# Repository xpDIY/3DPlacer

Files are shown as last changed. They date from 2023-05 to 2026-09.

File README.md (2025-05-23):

# 3DPlacer
3DPlacer is an adapter to convert 3D printer into pick and place machine that used 
for mounting SMT component into PCB. The aim is to make life easier for people who DIY their PCB 
and doesn't want to spend >$1k. While cost is low, the project still aim to bring enough accuracy
to mount tiny component (ex. 0201, 0402). Also one main goal is to make conversion simple and straight 
forward so that user can switch between 3D printing and PnP function in couple of minutes.
## Features
* Part rotation
* Airpump connectivity
* Adaptability for different 3D printers
  - Ender3 v2
  - Anycubic Mega SE
  - Ender CR10
  - Kingroon kp3s pro s1
* Compatible with openpnp
* Standard Lego style build plate supporting good extendability
* 30+ feeder can be mounted on 220x220mm plate
* 3D printed nozzle tip and JUKI nozzle tip supported
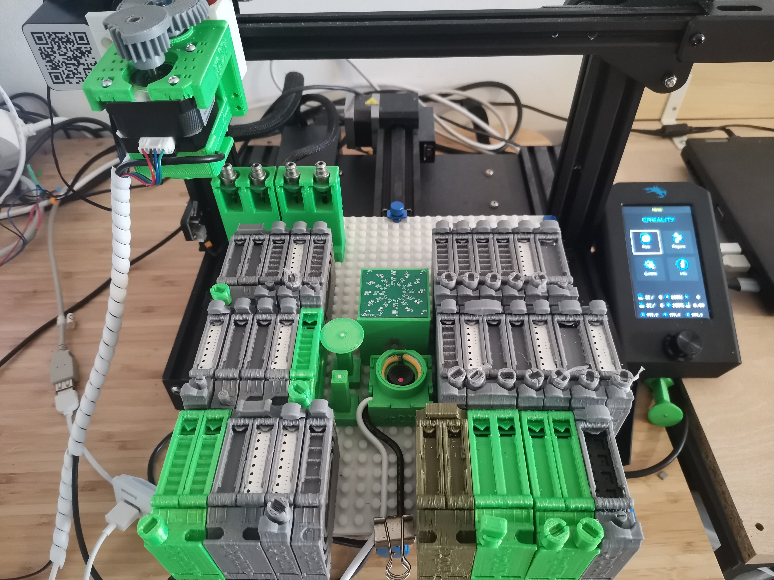
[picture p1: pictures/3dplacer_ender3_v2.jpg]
3DPlacer for Ender3 v2


## Software
* Position aware feature supported
* Both controller and feeder firmware included

### Usage

#### Pre-requsite
* DapLink or other programming interface support ARM M0 MCU with SWD interface
* clang compiler installed

#### Compile
* Enter sw/feeder or sw/control folder
* make clean
* make

#### Flash
* Make sure programmer is connected correctly to SWD interface
* run command `make flash`

## Contribution

Any contribution will be appreciated!

* If you see any bug or improvement, feel free to create a pull request and explain about the pull request

## References

The software project use PY32F0 template project as starting point, please refer to https://github.com/IOsetting/py32f0-template for detailed information.

Thanks and enjoy!

For more info, please refer to https://xpdiy.io
Youtube channel: https://www.youtube.com/@xpdiy

Shield: [][cc-by-nc-sa]

This work is licensed under a
[Creative Commons Attribution-NonCommercial-ShareAlike 4.0 International License][cc-by-nc-sa].

[][cc-by-nc-sa]

[cc-by-nc-sa]: http://creativecommons.org/licenses/by-nc-sa/4.0/
[cc-by-nc-sa-image]: https://licensebuttons.net/l/by-nc-sa/4.0/88x31.png
[cc-by-nc-sa-shield]: https://img.shields.io/badge/License-CC%20BY--NC--SA%204.0-lightgrey.svg

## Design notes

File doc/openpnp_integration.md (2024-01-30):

# This document describe the way to integrate with Openpnp

## General description
In order to integrate with Openpnp, the idea is to provide various G code so that openpnp can use and setup the system. The serial text interface will be used. There are several gcodes currently needed for integration. In the description below, square bracket [] means optional, {} means parameter. 

## System architecture
The system contains openpnp, strip board and components. When user starts job or setup the components in openpnp, ex. feeders, openpnp will fire command (described in section below), then the command string will be passed to strip boards, strip boards will be responbile to pass the strings further to peticular components. The components received the command will then interpret the command and send the response back. The strip board will be used as a tunnel which forward the infomation.
Communication between Openpnp and strip board is serial communication. Strip board can communicate with other strip boards, the protocol used here is I2C. Then under each strip board, there will be multiple components, in order to save space, 1 wire UART is used. The position sensing is achieved by resistor dividing, with 3.3v supply voltage, depend on position, it will sense max 50 positions, each position can have 66 mv gap which gives enough space for detecting the position consistently.

```mermaid
flowchart LR
Openpnp <--gcode--> ControlBoard <--uart--> StripPCB1
ControlBoard<--uart-->StripPCB2
ControlBoard<--uart--> ...
ControlBoard<--uart-->StripPCBn
StripPCB1<--1w-->Feeder1_1
StripPCB1<--1w-->Feeder1_2
StripPCB1<--1w-->Feeder1_X

StripPCB2<--1w-->Feeder2_1
StripPCB2<--1w-->Feeder2_2
StripPCB2<--1w-->Feeder2_X

StripPCBn<--1w-->Feedern_1
StripPCBn<--1w-->Feedern_2
StripPCBn<--1w-->Feedern_X

```

## GCodes
### M115
Firmware information code, this is used to make sure the openpnp can read the firmware therefore can use the I&S (issue and solution) wizard for better support setting up the machine.
  #### Usage
  ```
  M115
  ```
  #### Returns 
  ```
  Firmware name + version
  ```
  #### Example
  ```
  3DPlacer FIRMWARE v.01
  ```

### M888
Used to read back component info, ex. feeder, fiducial, camera etc. If no component id specified, then it will return all component info, components info will be returned as an array of components, each component will be separated by semicolon (;), the line ending will be CRLF.
  If component id specified, then it will return that specific component info
  Information included in the return of gcode contains (for different component, field will be different, the mandatary ones are name, position, type, id)
  
  * **type** - t: type, can be **<fed, fid, cam, chg, stp,lig>**, this can be extended, fed: feeder, fid:fiducial, cam: camera, chg: change station, stp: strip board, lig:light
  * **id** - id: id of component, will be unique accorss all components
  * **position**  - r: row, c: column, tr:total row, tc: total column
  * **dimension** - w: width, l: length, h: height
  * **name** - n: name ```Note: the name will be used for searching the component id```
  * **status** - st: status, general ones are **<ok, err>**, different component can have different status, ex. feeder can have **<end, jam>**, light can have **<on,off>**
  * **content** - tw: tape width, ex. 8, 12, 16..
  * **operate offset**: ox: offset x, oy: offset y, oz: offset z, this is the offset from contact point of the slot. For feeder, this means pick position, for camera, this means camera center position. For fiducial, this means the fiducial mark position.

  #### Component specific field
  * Feeder - feeder can have some specific fields
    * p: pitch, depend on tape inside, it can have 2mm, 4mm, or other pitch
    * ad: tape advance, if not zero, means it is advancing, when finish advancing, it will be reset to 0,  this field can be used to control advacning. ex. ad:1 means advance 1 pitch, see M887 gcode, ad:-1 means travel back 1 pitch position
    * st: status of feeder can be **<ok,err,end,jam>**, ok:good, err:unknown err, end:tap ended, jam: tap jammed
  * Light - light can have some specific status
    * st: status of light can be **<on, off>**. The light can be on or off. The on/off can be used as status, and also as control. See M887 for detial.
   
  #### Usage
  ```
  M888 [R:{row},C:{col},TR:{total row},TC:{total col};]
  ```
  #### Examples  
  ```
  M888 R:4,C:2; returns t:fed,id:12345678,w:12,l:64,h:43,ox:-5,oy:-2.1,tw:8,st:ok,r:4,c:2,n:100kohm

  ; below command returning all components separated by semicolon (;)
  M888;returns t:fed,id:12345678,w:12,l:64,h:43,ox:-5,oy:-2.1,tw:8,st:ok,r:4,c:2,n:100kohm; t:fed,id:12345679,w:16,l:64,h:43,ox:-5,oy:-4.1,tw:8,st:ok,r:3,c:2,n:100uf; t:fid,id:22222222,w:12,l:12,h:43,r:1,c:1,ox:3,oy:3,n:pri; t:fid,id:33333333,w:12,l:12,h:37,r:10,c:10,ox:3,oy:3,name:sec; t:cam,id:44444444,w:32,l:32,h:43,r:10,c:10,ox:8,oy:8,name:bot; t:lig,id:55555555,r:1,c:1,st:on,n:top; t:lig,id:66666666,r:5,c:5,st:off,n:bot[CRLF]
  ```

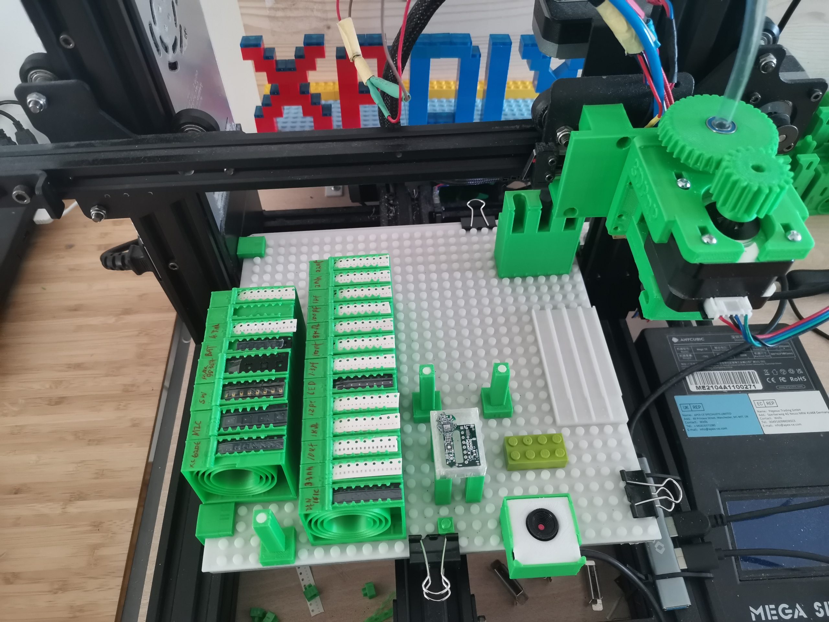
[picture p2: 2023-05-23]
pictures/3dpnp_mega_se.jpg

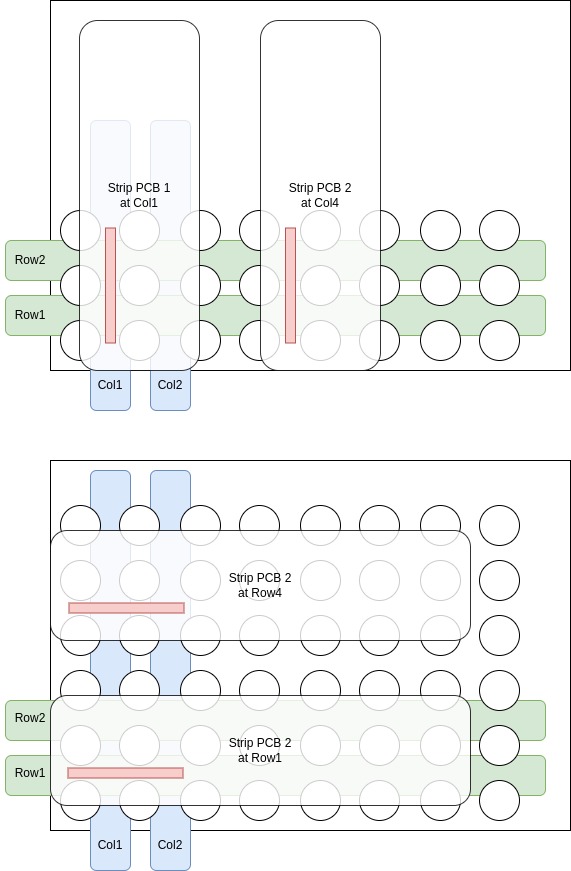
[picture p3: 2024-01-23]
pictures/rowAndColumnForBaseplate.jpg

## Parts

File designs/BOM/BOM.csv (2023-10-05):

partName | belongToComponent | spec | quantity | example model | example link #1 | example link #2 | comments
USB bottom camera | bottom camera | >1m pixel,64-70 degree,2.8-3.5mm focal length,25x30mm(w x h),<15mm height | 1 | OV9726,OV3660 | https://www.aliexpress.com/item/1005004818238391.html |  | OV3660 is 3m pixel choose 64 deg/3.5mm focal option, OV9726 is cheaper 1m pixel choose 70 deg/2.8mm focal option
USB top camera | nozzle head bundle (advanced version) | >1m pixel,64-70 degree,2.8-3.5mm focal length,25x30mm(w x h),<15mm height | 1 | OV9726,OV3660 | https://www.aliexpress.com/item/1005003937144930.html
stepper motor | nozzle head bundle (all versions) | Nema 17 stepper motor,<=30mm height,<=1.8deg angle,5mm shaft diameter,>10mm shaft length | 1 |  | https://www.aliexpress.com/item/1005005164124079.html | https://www.ebay.com/itm/234892079577 | 42x42mm frame size
stepper motor screw | nozzle head bundle (all versions) | M3 screw | 4 |  |  |  | M3x12mm
spring | nozzle head bundle (all versions) | 18mm outer diameter,1mm wire diameter,30mm length | 1 |  | https://www.aliexpress.com/item/1005004065500359.html | https://www.ebay.de/itm/393049700652
nozzle bearing | nozzle head bundle (all versions) | 10x15x4mm (10mm inner diameter,15mm outer diameter,4mm height) for JUKI nozzle | 1 | 6700 | https://www.aliexpress.com/item/1005004995124056.html | https://www.ebay.com/itm/266153229515
nozzle bearing | nozzle head bundle (all versions) | 15x21x4mm (15mm inner diameter,21mm outer diameter,4mm height) for JUKI nozzle | 1 |  | https://www.aliexpress.com/item/32955968366.html | https://www.ebay.com/itm/266153229485
air pump bearing | nozzle head bundle (all versions) | 6x12x4mm (6mm inner diameter,12mm outer diameter,4mm height) | 1 | MR126 | https://www.aliexpress.com/item/1005004222832036.html | https://www.ebay.com/itm/325608036967
sealing rubber O-ring | nozzle head bundle (all versions) | 5mm inner diameter,9mm outer diameter,2mm height (CS) for JUKI nozzle | 1 |  | https://www.aliexpress.com/item/1005004821149682.html
air pump | air pump | 12V mini air pump, >=4L/min flow, with in+out air flow, 4mm diameter for air intake | 1 | 370 model | https://www.aliexpress.com/item/33006096807.html
air pump tube | air pump | 6mm outer diameter,4mm inner diameter | 1 |  | https://www.aliexpress.com/item/1005004782664605.html
high power resistor | air pump | 10ohm for 12V printer,20ohm for 24V printer,>=10W | 1 |  | https://www.aliexpress.com/item/1005001792449275.html |  | depends on printer: 12V or 24V for part cooling fan. Limit the max current with high power resistor in series to air pump
LED strip | bottom camera | COB,5V,5mm width,white | 2 |  | https://www.aliexpress.com/item/1005003307581709.html |  | one for bottom camera, one for top camera, total<=0.5m cut to size

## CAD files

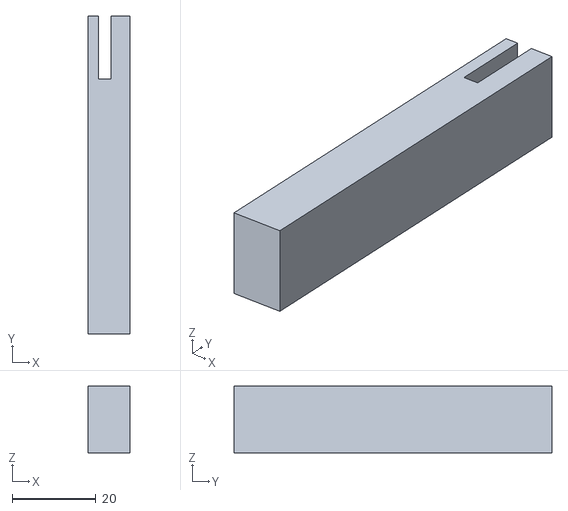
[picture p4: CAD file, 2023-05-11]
designs/adapters/cr10/home_position_extender_cr10.stl
10.0 x 76.0 x 16.0

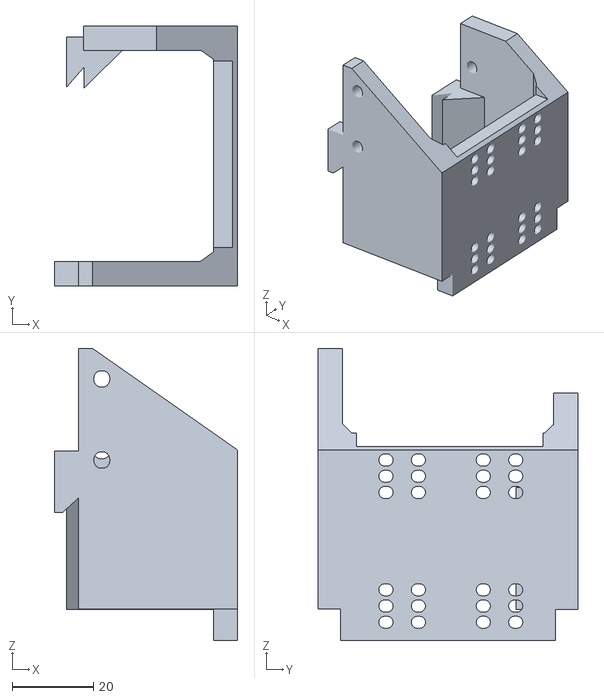
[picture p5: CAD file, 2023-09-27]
designs/adapters/kp3spro_s1/adapter_kp3spro_s1.stl
45.2 x 64.1 x 72.0

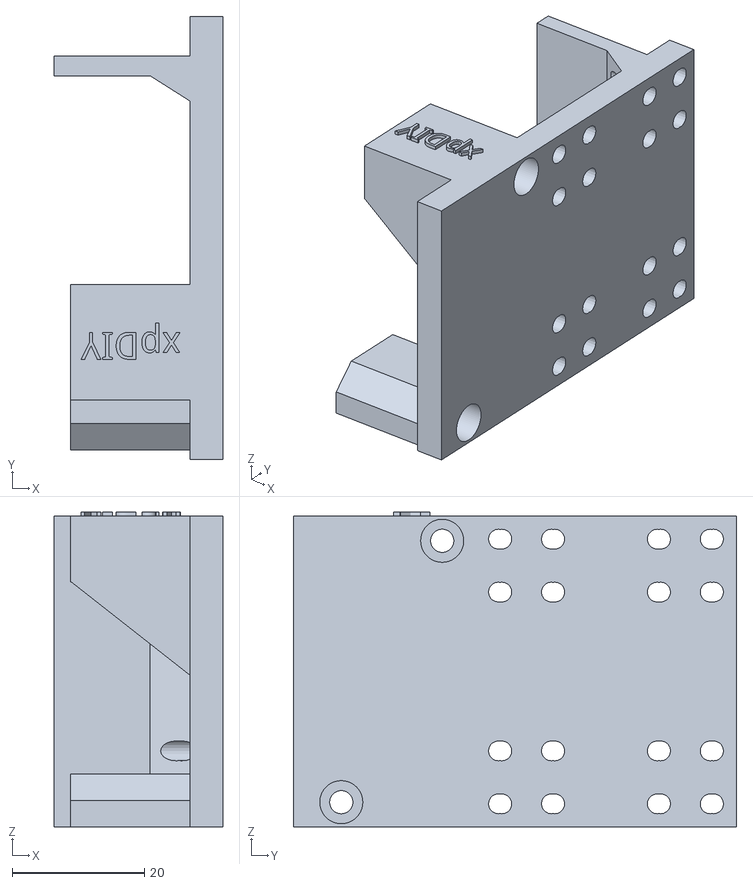
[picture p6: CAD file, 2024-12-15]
designs/adapters/mega_zero/adapter_anycubic_mega_zero.stl
25.5 x 67.0 x 47.6

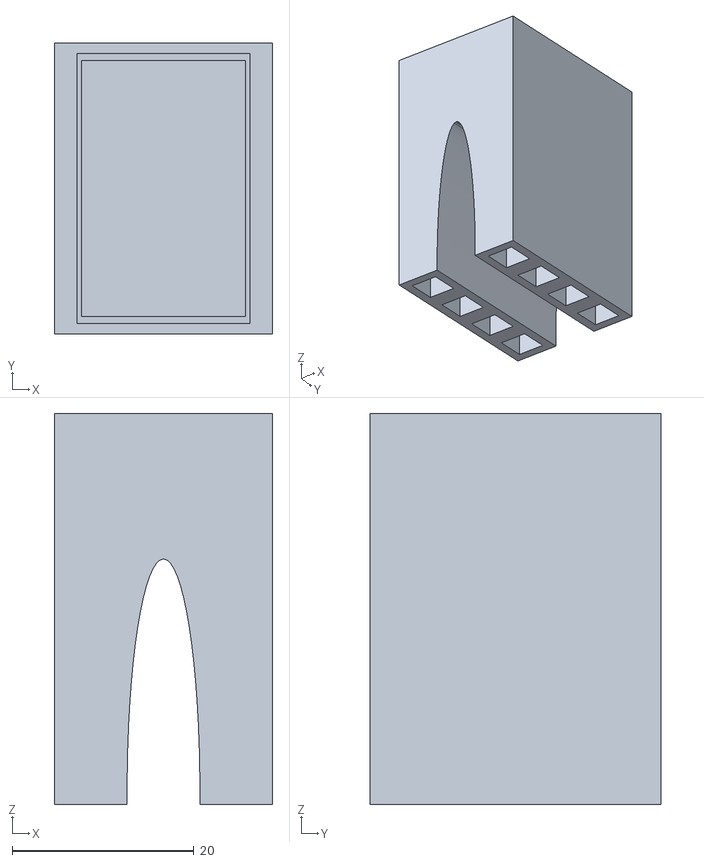
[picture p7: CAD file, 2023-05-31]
designs/board_fixture/board_fixture_32mm_24mm.stl
24.0 x 32.0 x 43.0

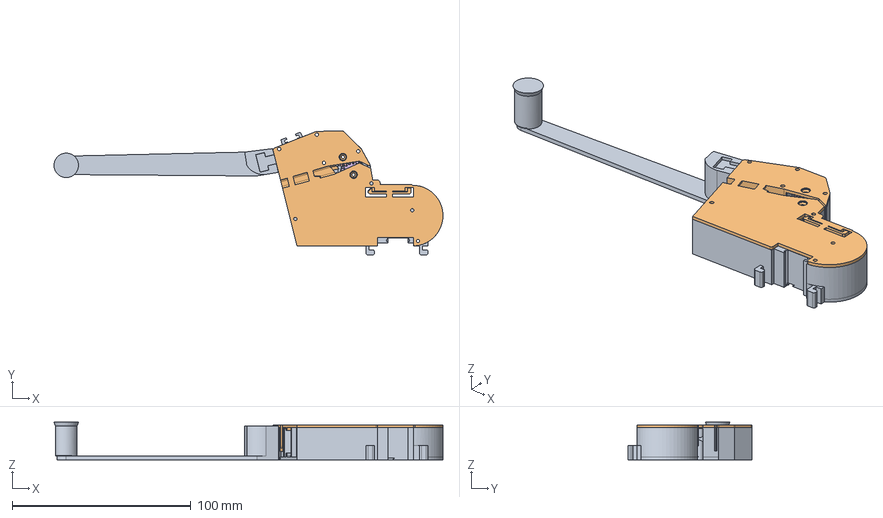
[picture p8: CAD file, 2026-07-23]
designs/feeders/cassetteAutoFeeder.FCStd
217.8 x 69.3 x 21.0 mm
bodyBottom
bodyCover
tapeDrivingGear
drivingGearSmall
onedirGear
gearOneDirManual

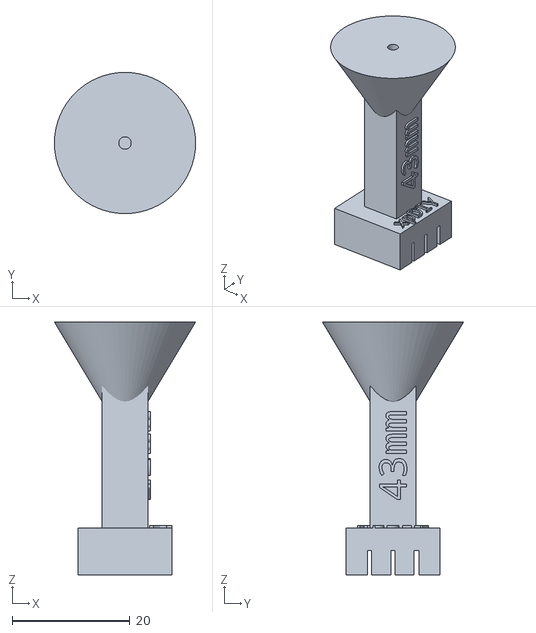
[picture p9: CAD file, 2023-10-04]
designs/fiducials/calibFid43mmPlatform.stl
24.0 x 24.0 x 43.0

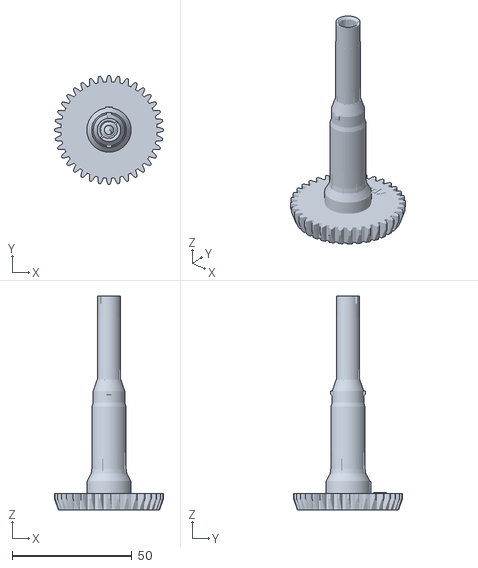
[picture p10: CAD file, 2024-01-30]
designs/nozzle_head_bundle/nozzle.stl
45.6 x 45.6 x 89.5

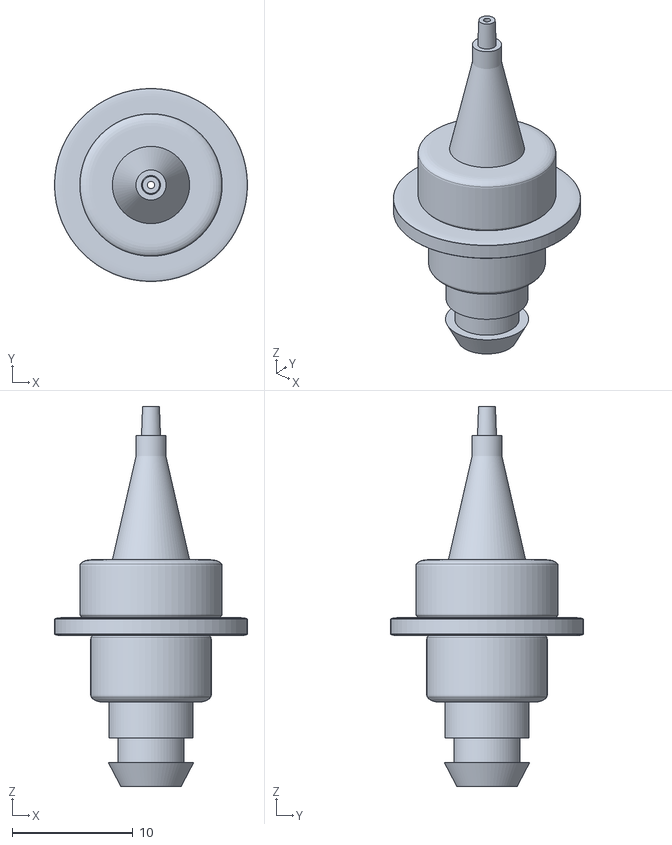
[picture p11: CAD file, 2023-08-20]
designs/nozzle_tips/nozzleTipJukiCompatible_0.6mm.stl
16.0 x 16.0 x 31.5

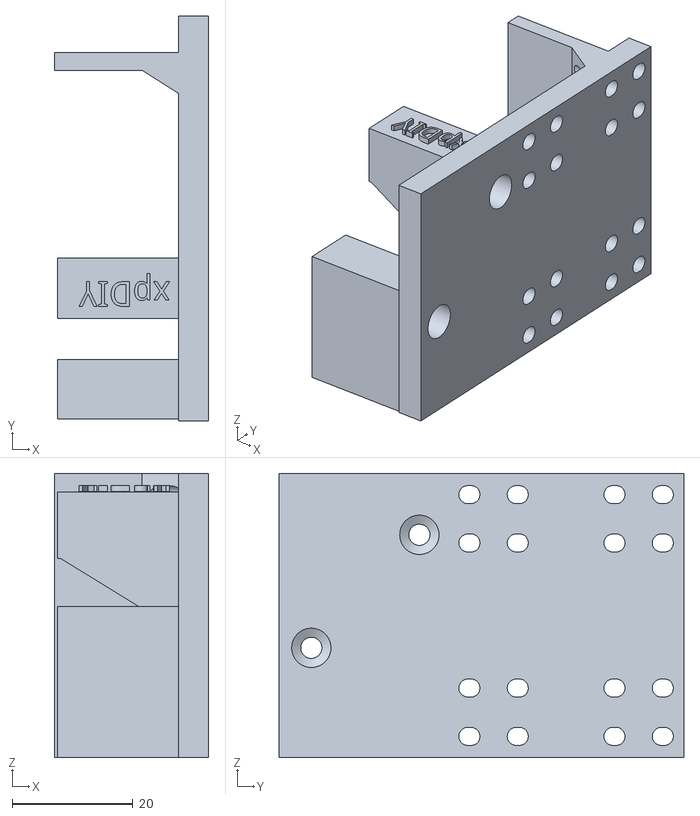
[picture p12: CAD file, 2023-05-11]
designs/adapters/cr10/adapter_ender3_cr10.stl
25.5 x 67.0 x 47.0

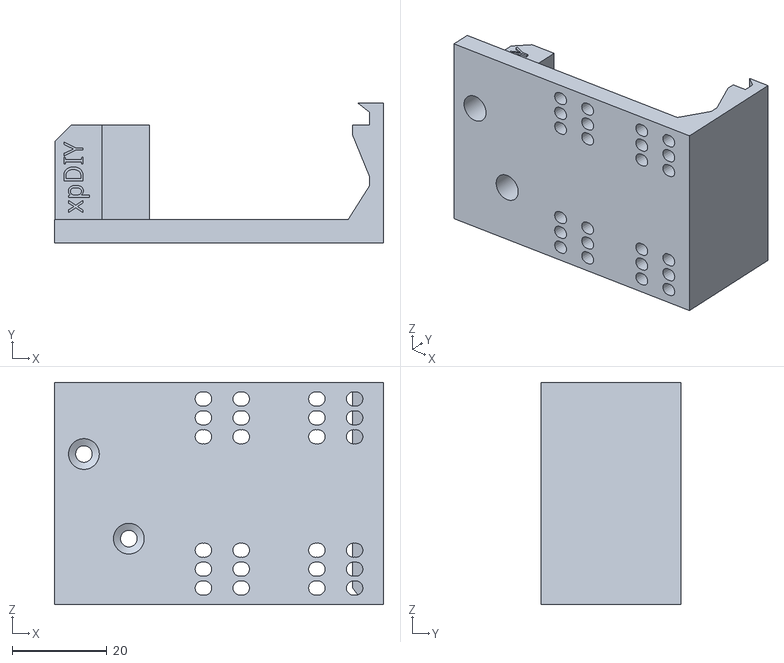
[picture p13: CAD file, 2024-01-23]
designs/adapters/ender3v2/adapter_ender3v2.stl
69.6 x 29.7 x 47.0

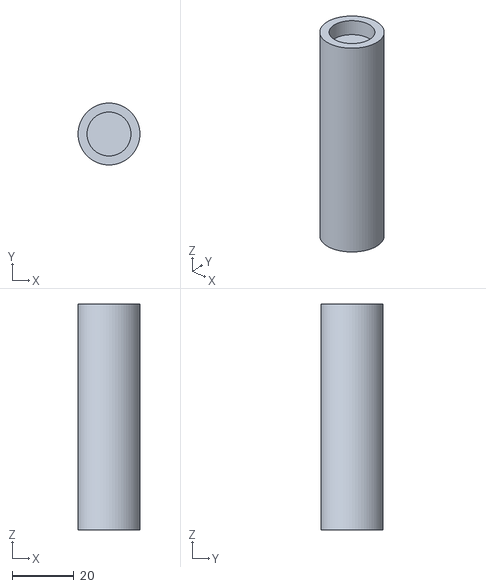
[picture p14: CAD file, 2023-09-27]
designs/adapters/kp3spro_s1/home_position_extender_kp3spro_s1.stl
20.0 x 20.0 x 73.0

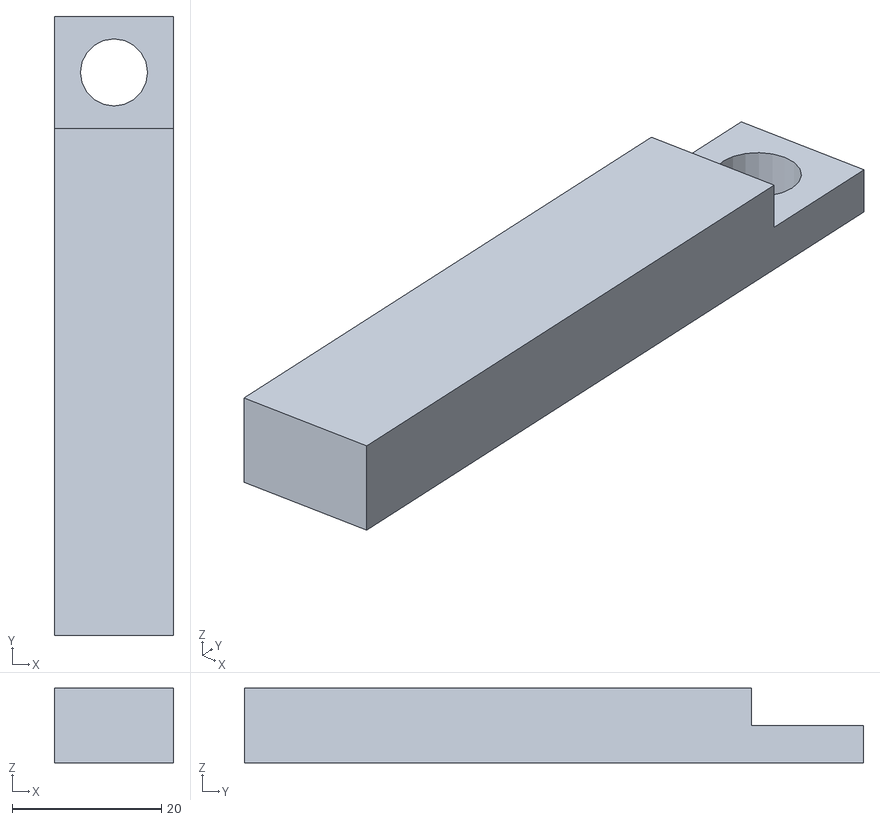
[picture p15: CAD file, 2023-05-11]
designs/adapters/mega_zero/home_position_extender_mega_zero.stl
16.0 x 83.0 x 10.0

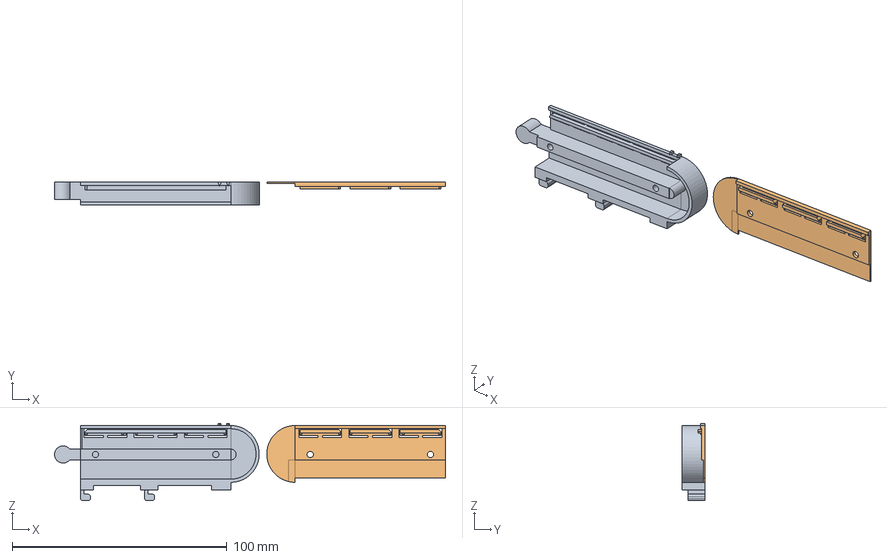
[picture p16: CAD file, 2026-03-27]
designs/feeders/stripFeederReturn.FCStd
182.1 x 10.5 x 36.0 mm
Body001 (Mirror #1)

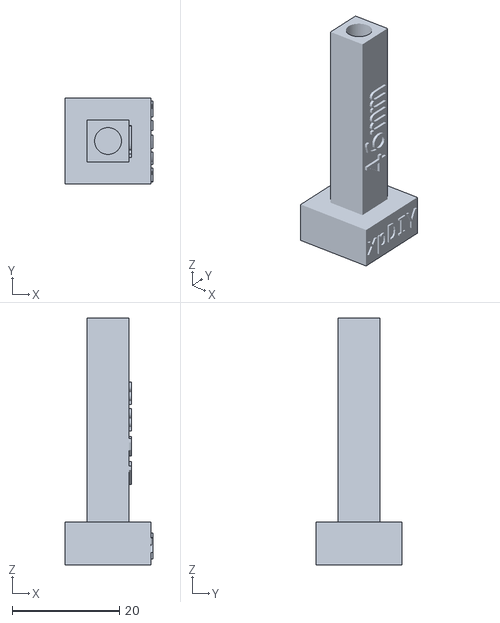
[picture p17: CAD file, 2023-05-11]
designs/fiducials/calibFid46mm.stl
16.4 x 16.0 x 46.0

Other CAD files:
designs/adapters/ender3v2/home_position_extender_ender3v2_2.7mmGap.stl
designs/nozzle_head_bundle/nozzleHeadFrame_Lite.stl
designs/nozzle_tips/nozzleTipJukiCompatible_4mm.stl
designs/adapters/ender3v2/home_position_extender_ender3v2_2.9mmGap.stl
designs/feeders/CassetteFeeder_16mm_v1.stl
designs/feeders/cassetteFeederTrimmer.stl
designs/feeders/cassetteFeederTrimmer_8mm_A.stl
designs/feeders/cassetteFeederTrimmer_8mm_B.stl
designs/feeders/cassetteFeederTrimmer_key.stl
designs/feeders/cassetteFeederv1_8mm_left.stl
designs/feeders/cassetteFeederv1_8mm_right.stl
designs/feeders/trimmer.stl
designs/fiducials/calibFid37mm.stl
designs/fiducials/calibFid40mm.stl
designs/fiducials/calibFid43mm.stl
designs/fiducials/calibMark.stl
designs/nozzle_head_bundle/nozzleFixture.stl
designs/nozzle_head_bundle/nozzleGear.stl
designs/nozzle_tips/nozzleTipV2_0.6mm.stl
designs/nozzle_tips/nozzleTipv2_4mm.stl

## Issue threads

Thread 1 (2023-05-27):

Interchangeable head

Sylensky, 2023-05-27:
Hi,
Awesome work you did there with the 3DPlacer, absolutely loving it!
Do you have future plans to make the printer head interchangeable?
From the firmware perspective it would be awesome to have a pnp function included in the 3d printers firmware but thats a topic for another long story..

How successfull in terms of accurracy have you been so far with 0201 components?

xpDIY, 2023-05-28:
Hi,
Thanks, I am looking for an easy way to switch, currently it can interchange between 3D printing and pnp with 2 screws, and require to adapt 2 fan wires, to go for full interchangeable, existing printer need to adapt also the hot end cable and temperature sensor and Bowden tube, I plan to first remove the need for 2 screws, then later full switch, but keep both options available.
For the placement, I got around 0.1mm accuracy without modifications on firmware of 3d printer, for me the 0201 could deviate a bit, but got pull back to pad during reflow, then I change the minimal step in Marlin fw(most of 3D printer combine several step to 1), then I got around 0.02 to 0.04mm) which is much better, so yes, fw itself also has room for adaptation regarding pnp functionality, I will make a video to show also about this topic.

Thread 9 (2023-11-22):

Empty layer when printing nozzle_Juki.stl

texruska, 2023-11-22:
There's a gap in the nozzle_Juki.stl file. Is it meant to be printed as 2 pieces?

xpDIY, 2023-11-22:
Thanks for spotting that, it is an issue. Now it is fixed, you can go to the full bundle and download again.

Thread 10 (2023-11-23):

Bottom camera casing doesn't match pictures

texruska, 2023-11-23:
Looks like the bottom camera casing file is out of date

Expected (from shop page):

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

Actual (after downloading):

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

You can see that there's nowhere for the camera cover to clip into

I would also double check the camera cover, too, just in case

xpDIY, 2023-11-23:
Thanks for feedback, this has been updated, could you get the latest version of download and give it a try?

texruska, 2023-11-23:
Thanks, that's all good now

I've also noticed that the nozzle head frame (Juki) is a different file to expected (notice where the top camera cover would go):

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

Can you tell that I'm in the process of building this? :)

xpDIY, 2023-11-23:
For this one, you can use the nozzleHeadFrame.stl included in the bundle, that one is the latest version, I should probably removed the old ones. Thanks for commenting!

texruska, 2023-11-23:
In that case issue closed 😎 I didn't even think to open the non-Juki file

Closed 2023-11-23.

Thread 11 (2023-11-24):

Top camera fitment into nozzle frame

texruska, 2023-11-24:
As discussed I printed the non-Juki nozzle head frame, but unfortunately the PCB for my top camera is too thick to slide in place (1.6mm):

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

Is it a tolerance issue on my side? I notice that the slot is wider than the PCB (PCB is 30mm wide)

xpDIY, 2023-11-24:
Hmm.. Ok, my camera board is thinner than what you have, I can make a
version with bigger slot width. But currently I am outside travelling, can
only do it tomorrow if that is ok.

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

xpDIY, 2023-11-24:
For 30mm width, can you print a calibration cube and check, just to be
sure. I leave around 0.6mm each side to hold the camera. I will be able to
help you tomorrow when I get back.

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

texruska, 2023-11-24:
That's okay. This is the 64deg OV3660 FYI, 30mmx25mm -- so the only difference is that it's thicker than yours (it fits in the bottom camera mount perfectly)

I think the width is okay if it's intentionally 1.2mm oversided, if I push it all the way to the side (like in the pic) then of course it won't sit in the other slot since they're the same depth

xpDIY, 2023-11-24:
Now I have updated the nozzle head frame to support 1.6mm top camera (with 0.2mm tolerance, so actually height is 1.8mm), you can download the full bundle and then find the updated head frame.

texruska, 2023-11-26:
Fits well, thanks :)

Closed 2023-11-26.

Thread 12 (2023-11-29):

Ender 3 v2 nozzle head adapter clash

0xBERNDOG, 2023-11-29:
It's not easy to show this, but the nozzle head adapter clashes with my gantry, causing the screw holes to not properly align

Misaligned bottom screw hole, excuse the shadows:
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

The clash:
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

I propose that we add a chamfer where the clash is to give some clearance while keeping it easily printable, I only need about 1-2mm more space

xpDIY, 2023-11-29:
Thanks for the idea, I have updated the product to include the chamfer, you can find it in https://www.xpdiy.io/product/nozzle-head-adapter-for-ender3v2-design-file/

0xBERNDOG, 2023-11-29:
Successful fix :)

Closed 2023-11-29.

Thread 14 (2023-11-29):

Ender 3 v2 failing to hit homing switch

0xBERNDOG, 2023-11-29:
It's hard to photograph this one, but my ender 3 v2 is missing the x-axis homing switch. I assume that the nozzle head adapter is supposed to hit it?

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

https://github.com/xpDIY/3DPlacer/assets/2800058/c9a0d3c2-87af-47b3-b61b-e6c95d8a9659

0xBERNDOG, 2023-11-29:
I think either a chamfer on the adapter (so the switch can be triggered by the metal bracket), or extend the adapter so that the adapter triggers the switch

At the moment the adapter clashes with the body of the switch while missing the lever

xpDIY, 2023-11-29:
Ok, it seems like the adapter hitting the x axis stop body, I think
the switch was supposed to hit the metal part, but somehow the adapter hit
it first. Let me make a chamfer for the adapter.
In the meantime, you can bend the thin metal piece of the homing switch to
make it stick a bit out so it hits the metal first.

I will make an adaption and upload.

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

xpDIY, 2023-11-29:
The new version has been uploaded, a chamfer is added. Also the home position extender I have put in an extra one with narrower gap so that it can adapt to different tolerance.

BTW, good to see you have the main components setup :)

0xBERNDOG, 2023-11-29:
Thanks, will print them both and update you

Except for these small issues, it's been a smooth process so far. I had been putting it off for ages

0xBERNDOG, 2023-11-29:
Fixed, and the homing extension fits snugly now

Closed 2023-11-29.

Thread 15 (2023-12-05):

LED channels not wide enough

0xBERNDOG, 2023-12-05:
In the nozzle head and bottom camera, the channel for the LEDs aren't wide enough for mine (I bought the ones from the BOM):

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

The strip is 8mm in width

xpDIY, 2023-12-05:
ok, I have updated the nozzle head bundle to add support for 8mm as well, you can download from the website.

0xBERNDOG, 2023-12-05:
Top camera fits well now, could you also adjust the bottom camera?

xpDIY, 2023-12-05:
I have also updated the bottom camera cover, you can download and give it a try!

0xBERNDOG, 2023-12-06:
Looks good to me thanks

Closed 2023-12-06.

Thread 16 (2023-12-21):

Nozzle suction

0xBERNDOG, 2023-12-21:
My pump has good suction, but it's all lost when going through the nozzle

Did you do anything in particular to seal it? I'm trying to diagnose where the losses are coming from

0xBERNDOG, 2023-12-21:
The most likely causes I can see:

* loose fit of the bearing at the top of the nozzle
* loose fit of the PTFE tube inside the bearing

xpDIY, 2023-12-21:
When you say lost suction, what do you mean? Do you have nozzle tip installed? There is no suction from the nozzle at all or only small amount of air coming from noze tip?

I didn't do anything special, when you fit the bearing on the top, is it tight? Also I have found sometimes the nozzle tip print out could have air leakage if not pirnted well, I normally connect the air output port of the pump and put the nozzle into water and check where is leaking. Or simply blowing into the nozzle while blocking the other end by hand to check if nozzle itself is leaking.

Sent from Outlook for Android<https://aka.ms/AAb9ysg>
________________________________
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

0xBERNDOG, 2023-12-21:
I identified the problem areas, and fixed it by modifying the mesh in fusion360:

1) The bearing was loose, so I made the hole 12.10mm diameter
2) My O-rings were actually 1.5mm tall, so they weren't sealing against the nozzle. I modified the end to pull the nozzle further down so that it properly squashes the O-ring

Now I can pick up my OpenPnP test pieces (hole punches) :)

xpDIY, 2023-12-22:
ok, glad it worked for you! I think it make sense to make parts with different tolerance..

0xBERNDOG, 2023-12-22:
A parametric model would work well, so the user can adjust the tolerance parameters

bonz099, 2024-02-28:
The new nozzle was a bit thin for me, and my printer sucks, so I dipped the whole lower part in conformal coating and let it drip dry. It has way better suction now.

xpDIY, 2024-02-28:
@bonz099 Thanks for the feedback, the tolearance is a challenge for different 3D printer, a parametric model will help in this case, I will see if I can provide something for that.

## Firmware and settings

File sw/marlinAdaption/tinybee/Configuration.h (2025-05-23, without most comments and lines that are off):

#pragma once
#define CONFIGURATION_H_VERSION 02000902
#define STRING_CONFIG_H_AUTHOR "(none, default config)" // Who made the changes.
#define SHOW_BOOTSCREEN
#define SERIAL_PORT 0
#define BAUDRATE 115200
#define SERIAL_PORT_2 -1
#define BAUDRATE_2 115200   // Enable to override BAUDRATE
  #define MOTHERBOARD BOARD_MKS_TINYBEE
#define LINEAR_AXES 5
#if LINEAR_AXES >= 4
  #define AXIS4_NAME 'A' // :['A', 'B', 'C', 'U', 'V', 'W']
#endif
#if LINEAR_AXES >= 5
  #define AXIS5_NAME 'B' // :['A', 'B', 'C', 'U', 'V', 'W']
#endif
#if LINEAR_AXES >= 6
  #define AXIS6_NAME 'C' // :['A', 'B', 'C', 'U', 'V', 'W']
#endif
#define EXTRUDERS 0
#define DEFAULT_NOMINAL_FILAMENT_DIA 1.75
#define TEMP_SENSOR_0 998
#define TEMP_SENSOR_1 998
#define TEMP_SENSOR_2 0
#define TEMP_SENSOR_3 0
#define TEMP_SENSOR_4 0
#define TEMP_SENSOR_5 0
#define TEMP_SENSOR_6 0
#define TEMP_SENSOR_7 0
#define TEMP_SENSOR_BED 1
#define TEMP_SENSOR_PROBE 0
#define TEMP_SENSOR_CHAMBER 0
#define TEMP_SENSOR_COOLER 0
#define TEMP_SENSOR_BOARD 0
#define TEMP_SENSOR_REDUNDANT 0
#define DUMMY_THERMISTOR_998_VALUE  25
#define DUMMY_THERMISTOR_999_VALUE 100
#define TEMP_RESIDENCY_TIME         10  // (seconds) Time to wait for hotend to "settle" in M109
#define TEMP_WINDOW                  1  // (°C) Temperature proximity for the "temperature reached" timer
#define TEMP_HYSTERESIS              3  // (°C) Temperature proximity considered "close enough" to the target
#define TEMP_BED_RESIDENCY_TIME     10  // (seconds) Time to wait for bed to "settle" in M190
#define TEMP_BED_WINDOW              1  // (°C) Temperature proximity for the "temperature reached" timer
#define TEMP_BED_HYSTERESIS          3  // (°C) Temperature proximity considered "close enough" to the target
#define TEMP_CHAMBER_RESIDENCY_TIME 10  // (seconds) Time to wait for chamber to "settle" in M191
#define TEMP_CHAMBER_WINDOW          1  // (°C) Temperature proximity for the "temperature reached" timer
#define TEMP_CHAMBER_HYSTERESIS      3  // (°C) Temperature proximity considered "close enough" to the target
#if TEMP_SENSOR_REDUNDANT
  #define TEMP_SENSOR_REDUNDANT_SOURCE    E1  // The sensor that will provide the redundant reading.
  #define TEMP_SENSOR_REDUNDANT_TARGET    E0  // The sensor that we are providing a redundant reading for.
  #define TEMP_SENSOR_REDUNDANT_MAX_DIFF  10  // (°C) Temperature difference that will trigger a print abort.
#endif
#define HEATER_0_MINTEMP   5
#define HEATER_1_MINTEMP   5
#define HEATER_2_MINTEMP   5
#define HEATER_3_MINTEMP   5
#define HEATER_4_MINTEMP   5
#define HEATER_5_MINTEMP   5
#define HEATER_6_MINTEMP   5
#define HEATER_7_MINTEMP   5
#define BED_MINTEMP        5
#define CHAMBER_MINTEMP    5
#define HEATER_0_MAXTEMP 275
#define HEATER_1_MAXTEMP 275
#define HEATER_2_MAXTEMP 275
#define HEATER_3_MAXTEMP 275
#define HEATER_4_MAXTEMP 275
#define HEATER_5_MAXTEMP 275
#define HEATER_6_MAXTEMP 275
#define HEATER_7_MAXTEMP 275
#define BED_MAXTEMP      150
#define CHAMBER_MAXTEMP  60
#define HOTEND_OVERSHOOT 15   // (°C) Forbid temperatures over MAXTEMP - OVERSHOOT
#define BED_OVERSHOOT    10   // (°C) Forbid temperatures over MAXTEMP - OVERSHOOT
#define COOLER_OVERSHOOT  2   // (°C) Forbid temperatures closer than OVERSHOOT
#define PIDTEMP
#define BANG_MAX 255     // Limits current to nozzle while in bang-bang mode; 255=full current
#define PID_MAX BANG_MAX // Limits current to nozzle while PID is active (see PID_FUNCTIONAL_RANGE below); 255=full current
#define PID_K1 0.95      // Smoothing factor within any PID loop
    #define DEFAULT_Kp  22.20
    #define DEFAULT_Ki   1.08
    #define DEFAULT_Kd 114.00
#define MAX_BED_POWER 255 // limits duty cycle to bed; 255=full current
#define MAX_CHAMBER_POWER 255 // limits duty cycle to chamber heater; 255=full current
  #define PID_FUNCTIONAL_RANGE 10 // If the temperature difference between the target temperature and the actual temperature
#define PREVENT_COLD_EXTRUSION
#define EXTRUDE_MINTEMP 170
#define PREVENT_LENGTHY_EXTRUDE
#define EXTRUDE_MAXLENGTH 200
#define THERMAL_PROTECTION_BED     // Enable thermal protection for the heated bed
#define THERMAL_PROTECTION_CHAMBER // Enable thermal protection for the heated chamber
#define THERMAL_PROTECTION_COOLER  // Enable thermal protection for the laser cooling
#define USE_XMIN_PLUG
#define USE_YMIN_PLUG
#define USE_ZMIN_PLUG
#define USE_IMIN_PLUG
#define USE_JMIN_PLUG
#define ENDSTOPPULLUPS
#define X_MIN_ENDSTOP_INVERTING false // Set to true to invert the logic of the endstop.
#define Y_MIN_ENDSTOP_INVERTING false // Set to true to invert the logic of the endstop.
#define Z_MIN_ENDSTOP_INVERTING false // Set to true to invert the logic of the endstop.
#define I_MIN_ENDSTOP_INVERTING false // Set to true to invert the logic of the endstop.
#define J_MIN_ENDSTOP_INVERTING false // Set to true to invert the logic of the endstop.
#define K_MIN_ENDSTOP_INVERTING false // Set to true to invert the logic of the endstop.
#define X_MAX_ENDSTOP_INVERTING false // Set to true to invert the logic of the endstop.
#define Y_MAX_ENDSTOP_INVERTING false // Set to true to invert the logic of the endstop.
#define Z_MAX_ENDSTOP_INVERTING false // Set to true to invert the logic of the endstop.
#define I_MAX_ENDSTOP_INVERTING false // Set to true to invert the logic of the endstop.
#define J_MAX_ENDSTOP_INVERTING false // Set to true to invert the logic of the endstop.
#define K_MAX_ENDSTOP_INVERTING false // Set to true to invert the logic of the endstop.
#define Z_MIN_PROBE_ENDSTOP_INVERTING false // Set to true to invert the logic of the probe.
#define X_DRIVER_TYPE  TMC2209_STANDALONE
#define Y_DRIVER_TYPE  TMC2209_STANDALONE
#define Z_DRIVER_TYPE  TMC2209_STANDALONE
#define I_DRIVER_TYPE  TMC2209_STANDALONE
#define J_DRIVER_TYPE  TMC2209_STANDALONE
#define DEFAULT_AXIS_STEPS_PER_UNIT   { 80, 80, 1600, 400, 400 }
#define DEFAULT_MAX_FEEDRATE          { 300, 300, 5, 25, 25 }
#define DEFAULT_MAX_ACCELERATION      { 200, 200, 50, 500, 500 }
#define DEFAULT_ACCELERATION          200    // X, Y, Z and E acceleration for printing moves
#define DEFAULT_RETRACT_ACCELERATION  500    // E acceleration for retracts
#define DEFAULT_TRAVEL_ACCELERATION   500    // X, Y, Z acceleration for travel (non printing) moves
#define DEFAULT_EJERK    5.0  // May be used by Linear Advance
  #define JUNCTION_DEVIATION_MM 0.013 // (mm) Distance from real junction edge
  #define JD_HANDLE_SMALL_SEGMENTS    // Use curvature estimation instead of just the junction angle
#define Z_MIN_PROBE_USES_Z_MIN_ENDSTOP_PIN
#define NOZZLE_TO_PROBE_OFFSET { 10, 10, 0 }
#define PROBING_MARGIN 10
#define XY_PROBE_FEEDRATE (133*60)
#define Z_PROBE_FEEDRATE_FAST (4*60)
#define Z_PROBE_FEEDRATE_SLOW (Z_PROBE_FEEDRATE_FAST / 2)
#define Z_CLEARANCE_DEPLOY_PROBE   10 // Z Clearance for Deploy/Stow
#define Z_CLEARANCE_BETWEEN_PROBES  5 // Z Clearance between probe points
#define Z_CLEARANCE_MULTI_PROBE     5 // Z Clearance between multiple probes
#define Z_PROBE_LOW_POINT          -2 // Farthest distance below the trigger-point to go before stopping
#define Z_PROBE_OFFSET_RANGE_MIN -20
#define Z_PROBE_OFFSET_RANGE_MAX 20
#define X_ENABLE_ON 0
#define Y_ENABLE_ON 0
#define Z_ENABLE_ON 0
#define E_ENABLE_ON 0 // For all extruders
#define I_ENABLE_ON 0
#define J_ENABLE_ON 0
#define DISABLE_X false
#define DISABLE_Y false
#define DISABLE_Z false
#define DISABLE_I false
#define DISABLE_E false             // Disable the extruder when not stepping
#define DISABLE_INACTIVE_EXTRUDER   // Keep only the active extruder enabled
#define INVERT_X_DIR false
#define INVERT_Y_DIR false
#define INVERT_Z_DIR false
#define INVERT_I_DIR false
#define INVERT_J_DIR false
#define INVERT_E0_DIR false
#define INVERT_E1_DIR false
#define INVERT_E2_DIR false
#define INVERT_E3_DIR false
#define INVERT_E4_DIR false
#define INVERT_E5_DIR false
#define INVERT_E6_DIR false
#define INVERT_E7_DIR false
#define X_HOME_DIR -1
#define Y_HOME_DIR -1
#define Z_HOME_DIR -1
#define I_HOME_DIR -1
#define J_HOME_DIR -1
#define X_BED_SIZE 400
#define Y_BED_SIZE 350
#define X_MIN_POS 0
#define Y_MIN_POS 0
#define Z_MIN_POS 0
#define X_MAX_POS X_BED_SIZE
#define Y_MAX_POS Y_BED_SIZE
#define Z_MAX_POS 100
#define I_MIN_POS 0
#define I_MAX_POS 360
#define J_MIN_POS 0
#define J_MAX_POS 360
#define MIN_SOFTWARE_ENDSTOPS
  #define MIN_SOFTWARE_ENDSTOP_X
  #define MIN_SOFTWARE_ENDSTOP_Y
  #define MIN_SOFTWARE_ENDSTOP_Z
  #define MIN_SOFTWARE_ENDSTOP_I
  #define MIN_SOFTWARE_ENDSTOP_J
  #define MIN_SOFTWARE_ENDSTOP_K
#define MAX_SOFTWARE_ENDSTOPS
  #define MAX_SOFTWARE_ENDSTOP_X
  #define MAX_SOFTWARE_ENDSTOP_Y
  #define MAX_SOFTWARE_ENDSTOP_Z
  #define MAX_SOFTWARE_ENDSTOP_I
  #define MAX_SOFTWARE_ENDSTOP_J
  #define MAX_SOFTWARE_ENDSTOP_K
#define MANUAL_I_HOME_POS 0
#define MANUAL_J_HOME_POS 0
#define HOMING_FEEDRATE_MM_M { (50*60), (50*60), (4*60), (4*60), (4*60) }
#define VALIDATE_HOMING_ENDSTOPS
#define EEPROM_SETTINGS     // Persistent storage with M500 and M501
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

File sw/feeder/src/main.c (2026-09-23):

#include "string.h"
#include "py32f0xx_hal.h"
#include "gparser.h"
#include "uart_control.h"
#include "feeder_control.h"
#include "py32f0xx_bsp_clock.h"
#include "configuration.h"

int idxMotor=0;
static void APP_GPIO_Config(void);
static void APP_SWC_AsInput_Config(void);


// Keep SWD alive briefly after power-up so the debugger can attach before
// SWCLK is reused as the SWC input. Keep this short so the feeder starts
// answering M888 soon after power-up.
#define SWD_GRACE_PERIOD_MS      2000U
#define STARTUP_MOTOR_RUN_MS     5000U

void APP_ErrorHandler(void)
{ 
  while (1);
}


int main(void)
{
  HAL_Init();
  uint32_t boot_tick = HAL_GetTick();
  BSP_HSI_24MHzClockConfig();                
  APP_GPIO_Config();
  //enable motor
  HAL_GPIO_WritePin(GPIOA,PIN_MOTOR_EN,GPIO_PIN_SET);
  // Boot indication: LED1 stays on until the feeder is ready to answer M888.
  HAL_GPIO_WritePin(GPIOA,PIN_LED1,GPIO_PIN_SET);
  HAL_GPIO_WritePin(GPIOB,PIN_LED2,GPIO_PIN_RESET);
  //This is for led push button
  read_feeder_data_from_flash();
  //USART2_Config();
  USART1_Config();
  APP_AdcConfig();
  HAL_HalfDuplex_EnableReceiver(&UartOwHandle);
  for(volatile int i=0;i<1000000;++i); //wait for voltage to stabilize
  init_adc();

  // Keep SWD available for a short window after power-up (no reset pin required).
  // Measured from boot, so the feeder is ready to answer M888 at
  // SWD_GRACE_PERIOD_MS after power-up (the ADC settle above is inside it).
  {
    uint32_t elapsed = HAL_GetTick() - boot_tick;
    if (elapsed < SWD_GRACE_PERIOD_MS)
    {
      HAL_Delay(SWD_GRACE_PERIOD_MS - elapsed);
    }
  }

  // Reuse SWCLK pin as active-low input for cover-tape position detect
  APP_SWC_AsInput_Config();

#if IS_AUTO_FEEDER
  // Power-on motor run: reverse direction and stop early when SWC is pulled low.
  // The loose-part feeder has no tape cover to home, so it skips this and is
  // ready to answer M888 as soon as the SWD grace period ends.
  motor_dir_forward = 0;
  start_motor();
  uint32_t startup_motor_tick = HAL_GetTick();
  while ((HAL_GetTick() - startup_motor_tick) < STARTUP_MOTOR_RUN_MS)
  {
    if (HAL_GPIO_ReadPin(GPIOA, PIN_SWC_IN) == GPIO_PIN_RESET)
    {
      break;
    }
  }
  stop_motor();
  motor_dir_forward = 1;
#endif

  // Ready to answer M888: turn off the boot indication.
  HAL_GPIO_WritePin(GPIOA, PIN_LED1, GPIO_PIN_RESET);

  //start_motor();
  /*
  if (HAL_UART_Receive_IT(&UartOwHandle, (uint8_t *)aRxBuffer, 1) != HAL_OK)
  {
    APP_ErrorHandler();
  }
  */
 
  while (1)
  {
    process_ow_data();
    process_feeder();
  }
}


static void APP_GPIO_Config(void)
{
  GPIO_InitTypeDef GPIO_InitStruct;

  __HAL_RCC_GPIOA_CLK_ENABLE();
  __HAL_RCC_GPIOB_CLK_ENABLE();

  GPIO_InitStruct.Pin = PIN_MOTOR_EN;
  GPIO_InitStruct.Mode = GPIO_MODE_OUTPUT_PP;
  GPIO_InitStruct.Pull = GPIO_PULLUP;
  GPIO_InitStruct.Speed = GPIO_SPEED_FREQ_HIGH;
  HAL_GPIO_Init(GPIOA, &GPIO_InitStruct);
  //adc pin for gpio 4
  GPIO_InitStruct.Pin = PIN_RPOS;
  GPIO_InitStruct.Mode = GPIO_MODE_ANALOG;
  GPIO_InitStruct.Pull = GPIO_NOPULL;
  HAL_GPIO_Init(GPIOA, &GPIO_InitStruct);  
//adc pin for gpio 5
  GPIO_InitStruct.Pin = PIN_CPOS;
  GPIO_InitStruct.Mode = GPIO_MODE_ANALOG;
  GPIO_InitStruct.Pull = GPIO_NOPULL;
  HAL_GPIO_Init(GPIOA, &GPIO_InitStruct);  

  GPIO_InitStruct.Pin = PIN_MOTOR_A1;
  GPIO_InitStruct.Mode = GPIO_MODE_OUTPUT_PP;
  GPIO_InitStruct.Pull = GPIO_PULLUP;
  GPIO_InitStruct.Speed = GPIO_SPEED_FREQ_HIGH;
  HAL_GPIO_Init(GPIOA, &GPIO_InitStruct);

  GPIO_InitStruct.Pin = PIN_MOTOR_A2;
  GPIO_InitStruct.Mode = GPIO_MODE_OUTPUT_PP;
  GPIO_InitStruct.Pull = GPIO_PULLUP;
  GPIO_InitStruct.Speed = GPIO_SPEED_FREQ_HIGH;
  HAL_GPIO_Init(GPIOA, &GPIO_InitStruct);

  GPIO_InitStruct.Pin = PIN_LED1;
  GPIO_InitStruct.Mode = GPIO_MODE_OUTPUT_PP;
  GPIO_InitStruct.Pull = GPIO_PULLUP;
  GPIO_InitStruct.Speed = GPIO_SPEED_FREQ_HIGH;
  HAL_GPIO_Init(GPIOA, &GPIO_InitStruct);  

  GPIO_InitStruct.Pin = PIN_LED2;
  GPIO_InitStruct.Mode = GPIO_MODE_OUTPUT_PP;
  GPIO_InitStruct.Pull = GPIO_PULLUP;
  GPIO_InitStruct.Speed = GPIO_SPEED_FREQ_HIGH;
  HAL_GPIO_Init(GPIOB, &GPIO_InitStruct);    

  GPIO_InitStruct.Pin = PIN_PART_LED;
  GPIO_InitStruct.Mode = GPIO_MODE_OUTPUT_PP;
  GPIO_InitStruct.Pull = GPIO_PULLUP;
  GPIO_InitStruct.Speed = GPIO_SPEED_FREQ_HIGH;
  HAL_GPIO_Init(GPIOB, &GPIO_InitStruct);    

  GPIO_InitStruct.Pin = PIN_PART_DET;
  GPIO_InitStruct.Mode = GPIO_MODE_INPUT;
  // PA12 (PD1): normally HIGH from interrupter, LOW when beam interrupted.
  // Keep internal pulldown so released line is read as LOW.
  GPIO_InitStruct.Pull = GPIO_PULLDOWN;
  GPIO_InitStruct.Speed = GPIO_SPEED_FREQ_HIGH;
  HAL_GPIO_Init(GPIOA, &GPIO_InitStruct);

  //for switch control
  GPIO_InitStruct.Pin = PIN_SW_B;
  GPIO_InitStruct.Mode = GPIO_MODE_INPUT;
  GPIO_InitStruct.Pull = GPIO_PULLUP;
  GPIO_InitStruct.Speed = GPIO_SPEED_FREQ_HIGH;
  HAL_GPIO_Init(GPIOA, &GPIO_InitStruct);    

}

static void APP_SWC_AsInput_Config(void)
{
  GPIO_InitTypeDef GPIO_InitStruct;

  GPIO_InitStruct.Pin = PIN_SWC_IN;
  GPIO_InitStruct.Mode = GPIO_MODE_INPUT;
  GPIO_InitStruct.Pull = GPIO_PULLUP;
  GPIO_InitStruct.Speed = GPIO_SPEED_FREQ_HIGH;
  HAL_GPIO_Init(GPIOA, &GPIO_InitStruct);
}

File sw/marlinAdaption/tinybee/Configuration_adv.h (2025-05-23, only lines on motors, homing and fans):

#define DUAL_NOZZLE
#define E0_AUTO_FAN_PIN -1
#define E1_AUTO_FAN_PIN -1
#define E2_AUTO_FAN_PIN -1
#define E3_AUTO_FAN_PIN -1
#define E4_AUTO_FAN_PIN -1
#define E5_AUTO_FAN_PIN -1
#define E6_AUTO_FAN_PIN -1
#define E7_AUTO_FAN_PIN -1
#define CHAMBER_AUTO_FAN_PIN -1
#define COOLER_AUTO_FAN_PIN -1
#define COOLER_FAN_PIN -1
#define HOMING_BUMP_MM      { 5, 5, 2, 2, 2 }       // (mm) Backoff from endstops after first bump
#define HOMING_BUMP_DIVISOR { 2, 2, 4, 4, 4 }       // Re-Bump Speed Divisor (Divides the Homing Feedrate)
#define MICROSTEP_MODES { 16, 16, 16, 16, 16, 16 } // [1,2,4,8,16]
#define LIN_ADVANCE
  #define LIN_ADVANCE_K 0.22    // Unit: mm compression per 1mm/s extruder speed

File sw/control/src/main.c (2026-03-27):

#include "string.h"
#include "py32f0xx_hal.h"
#include "gparser.h"
#include "uart_control.h"
#include "py32f0xx_bsp_clock.h"
#include "common.h"

static void APP_GPIO_Config(void);

void APP_ErrorHandler(void)
{ 
  while (1){
    for(int i=0;i<100;i++){
      HAL_GPIO_TogglePin(GPIOA, GPIO_PIN_5);
      HAL_Delay(100);
    }
  }
}

int main(void)
{
  HAL_Init();   
  BSP_HSI_24MHzClockConfig();                                              
  APP_GPIO_Config();
  parser_init();
  HAL_GPIO_WritePin(GPIOA,GPIO_PIN_5,GPIO_PIN_RESET);
  USART2_Config();
  USART1_Config();
  /*
  if (HAL_UART_Receive_IT(&UartHandle, (uint8_t *)aRxBuffer, 1) != HAL_OK)
  {
    APP_ErrorHandler();
  }
    */

  
  while (1)
  { 
    ReceiveUart();
    ProcessAMsg();
  }
}

static void APP_GPIO_Config(void)
{
  GPIO_InitTypeDef GPIO_InitStruct;

  __HAL_RCC_GPIOA_CLK_ENABLE();
  // PA5
  GPIO_InitStruct.Pin = GPIO_PIN_5;
  GPIO_InitStruct.Mode = GPIO_MODE_OUTPUT_PP;
  GPIO_InitStruct.Pull = GPIO_PULLUP;
  GPIO_InitStruct.Speed = GPIO_SPEED_FREQ_HIGH;
  HAL_GPIO_Init(GPIOA, &GPIO_InitStruct);

  GPIO_InitStruct.Pin = GPIO_PIN_12;
  GPIO_InitStruct.Mode = GPIO_MODE_OUTPUT_PP;
  GPIO_InitStruct.Pull = GPIO_PULLUP;
  GPIO_InitStruct.Speed = GPIO_SPEED_FREQ_HIGH;
  HAL_GPIO_Init(GPIOA, &GPIO_InitStruct);

  GPIO_InitStruct.Pin = GPIO_PIN_6;
  GPIO_InitStruct.Mode = GPIO_MODE_INPUT;
  GPIO_InitStruct.Pull = GPIO_NOPULL;
  GPIO_InitStruct.Speed = GPIO_SPEED_FREQ_HIGH;
  HAL_GPIO_Init(GPIOA, &GPIO_InitStruct);
}

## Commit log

2023-05-11 add core designs, including nozzle head bundle, nozzle tips, fiducials, feeders, base plate and adapters for both anycubic mega zero and ender cr10
    [CassetteFeeder_16mm_v1.stl, adapter_anycubic_mega_zero.stl, adapter_ender3_cr10.stl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]
2023-05-11 move the adapter to corresponding folder
    [adapter_anycubic_mega_zero.stl, adapter_ender3_cr10.stl, home_position_extender_cr10.stl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]
2023-05-11 added supported 3D printer model
2023-05-23 added BOM to include parts that is not 3D printed
    [BOM.csv]
2023-05-26 added cassette feeder trimmer version
    [cassetteFeederTrimmer.stl]
2023-05-29 Create Baseplate-210x210mm.stl
    Added a 210x210mm base plate file for printers with 220mm print beds.
2023-05-31 add example board fixture of 32mm x 24mm
    [board_fixture_32mm_24mm.stl]
2023-07-11 improved cassetteFeeder Trimmer and nozzle design
    [cassetteFeederTrimmer.stl, nozzle.stl]
2023-07-26 add support for JUKI nozzle.
    [nozzleFixture_Juki.stl, nozzleHeadFrame_Juki_Lite.stl, nozzle_Juki.stl]
2023-07-29 added support for ender3v2 3D printer
    [adapter_ender3v2.stl, home_position_extender_ender3v2.stl]
2023-07-29 Update README.md
    added support for ender3v2 3D printer
2023-08-20 various improvements: 1. nozzle head frame with optimized thermo performance. 2. nozzle tips - with Juki nozzle compatibility.
    [nozzleHeadFrame_Juki_Lite.stl, nozzleTipJukiCompatible_0.6mm.stl, nozzleTipJukiCompatible_4mm.stl]
2023-09-27 added adapter for kp3spro s1
    [adapter_kp3spro_s1.stl, home_position_extender_kp3spro_s1.stl]
2023-10-04 1.updated BOM to include the detail part with example link. 2.added calibration fiducial that supports nozzle tip to camera offset
    [BOM.csv, calibFid43mmPlatform.stl]
2023-10-05 updated BOM to add the outer diameter of the spring
    [BOM.csv]
2023-10-05 1.updated BOM for example links with shorter form. 2. corrected specification of some parts. Thanks for Nikki for checking and updating.
    [BOM.csv]
2023-10-19 1. Added the latest version of cassetteFeederTrimmer, improve the stability and robustness. 2.Updated to the latest picture that shows the Ender3 v2 adaption
    [cassetteFeederTrimmer_8mm_A.stl, cassetteFeederTrimmer_8mm_B.stl, cassetteFeederTrimmer_key.stl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]
2023-11-22 fixed the issue that there is a gap for Juki nozzle
    [nozzle_Juki.stl]
2023-12-05 various improvements based on input: 1. retired non-juki nozzle support 2. improved Ender3v2 adapter to avoid collision to the home stop 3.improve home position extender for ender3v2 to account for t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
    [adapter_ender3v2.stl, home_position_extender_ender3v2.stl, home_position_extender_ender3v2_2.7mmGap.stl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]
2024-01-30 updated the nozzle component to use 1. friction for holding the nozzle tip for easier switch. 2. spring support adjusted to make it strong
    [nozzle.stl]
2024-12-15 updated anycubic mega zero adapter
    [adapter_anycubic_mega_zero.stl]
2025-01-17 initial commit for feeder and controller fw for position aware feeder feature, the py32f0 project structure please refer to https://github.com/IOsetting/py32f0-template
    [configuration.h]
2025-05-23 add software treaking for marlin to support pnp feature, with x,y,z and A,B axis
    [Configuration.h, Configuration_adv.h]
2026-03-15 removed the board
2026-03-17 add support for cassette loose feeder. Change structure of control to run in main loop instead of interrupt
    [configuration.h]
2026-03-17 fix the position reporting issue for feeder
    [feeder_control.c, m888.c]
2026-03-17 updated the feeder to support calibration of voltage and also set height
2026-03-27 add strip feeder for 3DPlacer v2
    [stripFeederReturn.FCStd]

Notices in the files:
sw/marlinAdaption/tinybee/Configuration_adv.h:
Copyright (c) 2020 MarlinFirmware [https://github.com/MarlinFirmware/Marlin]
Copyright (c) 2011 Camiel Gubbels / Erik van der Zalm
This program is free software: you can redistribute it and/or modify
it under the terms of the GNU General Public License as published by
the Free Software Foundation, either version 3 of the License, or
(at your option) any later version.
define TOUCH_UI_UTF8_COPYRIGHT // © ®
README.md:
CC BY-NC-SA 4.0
